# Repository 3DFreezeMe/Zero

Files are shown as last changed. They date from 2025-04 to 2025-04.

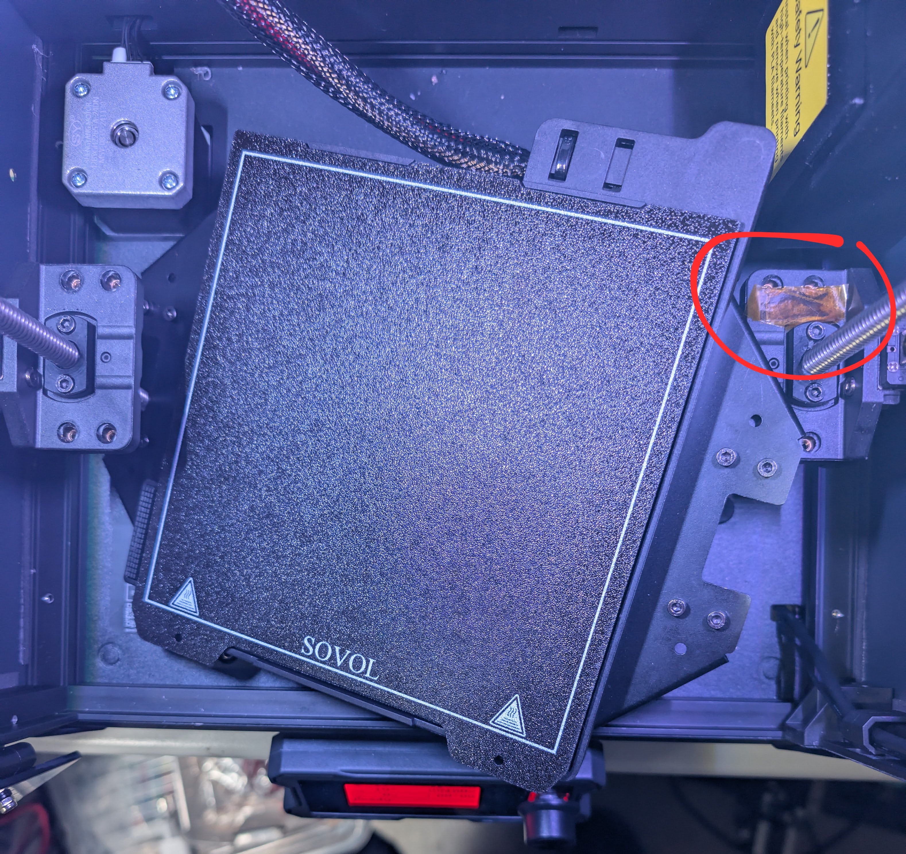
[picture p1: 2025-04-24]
F.jpg

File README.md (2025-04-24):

How to tram the bed of the Sovol Zero 3D printer
------------------------------------------------

The goal is to be able to rotate both left and right lead-screws freely and separately from each other.
That way you can rotate them until both blocks are pinched between bed and x gantry. Then the bed is level from left to right.

- turn off power and remove glass top and the metal bottom plate.
- tilt/turn the printer in a way you can easily reach belt and see the blocks (I just tilted and have it rest on the spool holder)

Pictures with instructions:

--------
METHOD 1
--------

A. 
- place blocks on both sides of extruder on X gantry

B. 
- you can move belt to lift bed upwards to X gantry if you want but this is how it will look after step D. below

C. 
- Step 1) and 2) ONLY WHEN NEEDED!
- I was able to just remove the belt from idler 3) by hand without loosening or removing any screw! Does not need much force.

1) loosen circled screws, no need to remove them
2) loosen screw (use the channel following the arrow)
   for me it was not needed to remove it but I completely loosened the screw
3) (push the idler left from 1) a bit to the left to release belt tension so that you can) remove the belt from idler 3)

D. 
- with the belt removed from idler 3) you are now able to rotate both lead-screws independently by hand until both blocks are pinched between bed and and x gantry

Finishing touches:

- put back belt around idler 3)
- (put back screw 2) if you loosened it completely from the hole)
- (tighten all screws)
- create new heightmap (http://<printer-ip>/heightmap) and verify if deviation is better 
- when happy with results put back bottom plate etc

--> now your bed should be reasonably level from left to right in parallel to the x gantry of the printer. Placing the belt back into position, the alignment could move a bit. Finer adjustments are easier using the belt-tooth-skipping method (next).

---------
METHOD 2:
---------

- using the belt-tooth-skipping technic for fine adjustments after using method above or just replacing it.
- maybe not for everyone but it is a tested and working method
- for explanation of procedure see video: https://youtu.be/GVRu_uX4PEk?si=_stUpJl4nDN17h4r
- in case of the Sovol Zero, you would do this underneath where the belt and couplers are located

- 

--------
SHIMMING
--------

E.
- idea for front to back tramming by shimming (washers or printed shims) in corners where bed is mounted to z lead-screws with 2 screws in each corner
  tightening/loosening them has some effect but with the speed this printer is capable of, I would rather not have loosened screws
  --> as these are quite close together, the effect off adding the needed 0.2mm on either front or back side will result in a bigger change over-all than wanted
- added 'zero-bed-shim.step' file for testing
- I tested with the lowest heights you could possibly print and tried these on the lowest side (back-side for me).
  But with a difference of let's say -0.2mm in your heightmap front to back, adding 0.2mm on both back left and right sides (under the screws in picture E.) the result is     bigger than you need.
- tested also by putting shims of 0.2mm under front screws and 0.3mm under back screws (so effectively 0.1mm added to back), the results were not what I hoped for.

F.
- upon further testing, shimming using Kapton tape will get you there. Very thin, heat resistant and therefor best option to get an even bed front to back.

--> after adding several layers of Kapton tape in the lowest corner, I ended up with a 0.102mm deviation heightmap (cold) and 0.089mm hot (20m soak @100C). See 'cold after tramming.jpg' and 'hot after tramming.jpg' for heightmap results after tramming.
Not sure why the z=0 point is almost 0.3mm lower when hot, I homed the printer after soak and before the new heightmap scan. Maybe because I did alter the tightness of screw with nylock nut which holds the strain gauge underneath left front corner.
- a reboot did not fix the z=0 results (first layer prints perfect)

G.
- Now the latest 1.4.2 firmware moves to using eddy sensor for z offset, maybe shimming the bed itself could be done without worrying about the pressure gauge underneath      the bed.

tbc

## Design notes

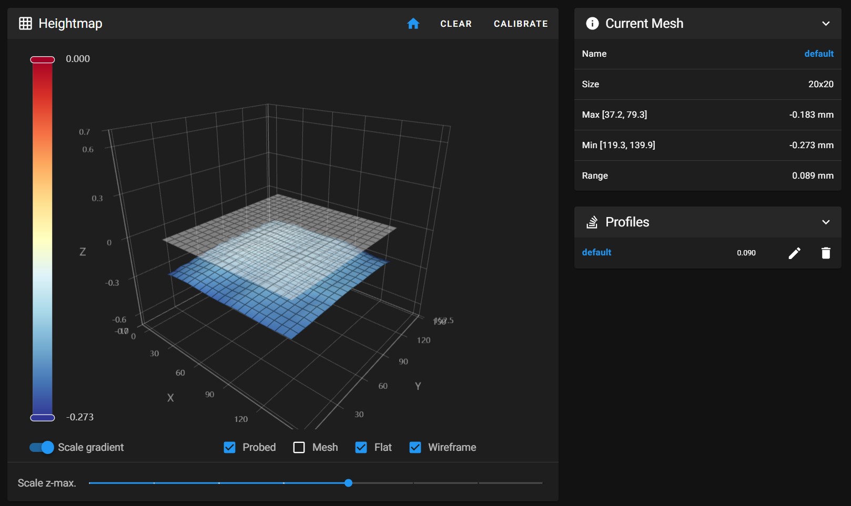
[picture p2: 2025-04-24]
hot after tramming.jpg

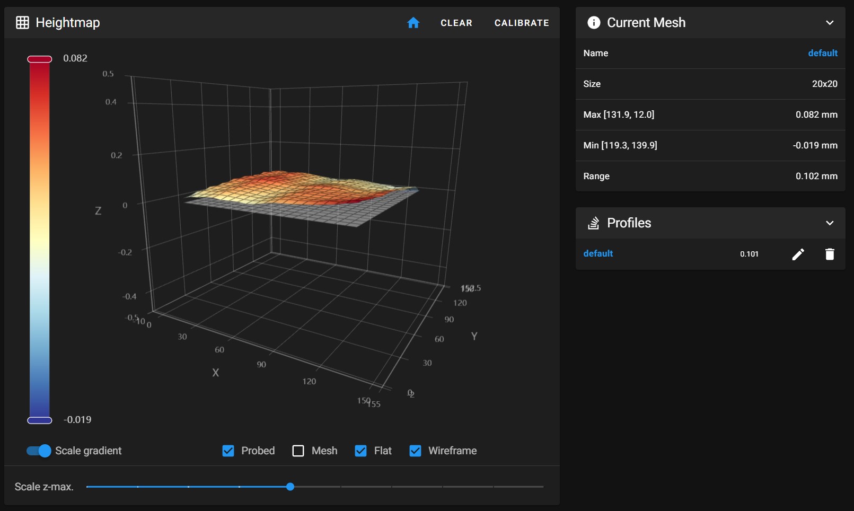
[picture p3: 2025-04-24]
cold after tramming.jpg

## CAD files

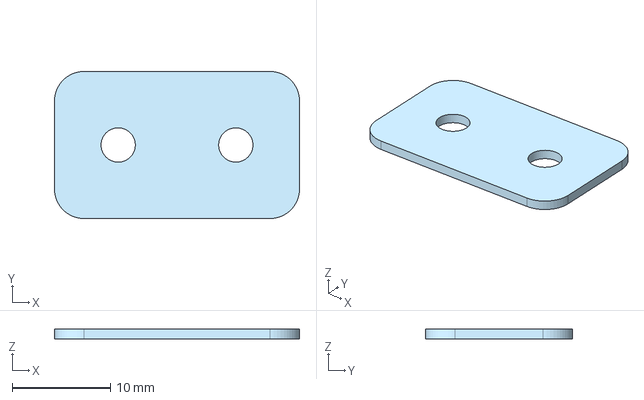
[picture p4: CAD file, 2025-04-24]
zero-bed-shim.step
25.0 x 15.0 x 1.00 mm

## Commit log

2025-04-23 how to tram bed for the Sovol Zero
2025-04-23 4 bed screws
2025-04-24 shim 0.2mm
    change (olny) z height in slicer and print several heights to test
    [zero-bed-shim.step]
